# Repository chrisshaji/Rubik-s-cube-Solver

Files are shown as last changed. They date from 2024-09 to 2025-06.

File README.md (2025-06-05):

# Rubik's Cube Solver

Fully 3-D printed rubik's cube solver that can solve a 3x3 rubik's cube.

## Design Rationale

The motor and cube connectors were the first pieces to be designed and fabricated. These pieces had to be tolerenced perfectly as if they were too loose, it would slip and too tight 
then it would be really hard to remove it. After a lot of testing and printing, I arrived at the perfect dimensions that ensure a smooth fit with minimal sliding. Moreover, in order
screw holes were implemented on the side in the offchance that these piece rub on each other and get loose after a lot of testing.

The main design constraint was coming up with a solution to securely harness each stepper motor to each face of the cube. Each motor weighs ~1 lb so 
so the column pieces had to be strong enough to support it while vibrating at max speed. The dimensions were measured using vernier calipers and a tolerance range of 8-10% was used.
I had also implemented a honeycomb design on the side for extra ventiliation. Finally, screw tabs were added so that motor can be screwed into the column. 

One goal I had with the base plate and the arch was to keep the filament usage down to a minimum. I have employed the use of pattern to hollow out these pieces so that less material would be used.
For the arch, I had initially envisioned to use neodynium magnets for easy removal of the cube. However, this proved not to be strong enough upon further testing, therefore I went with the good old 
screws and nuts on the side of the arch. For the base plate, similar design changes were made and each of the four columns, along with the bottom motor can be screwed directly onto the base plate.

<table align="center">
  <tr>
    <td style="padding-right: 30px;">
      Breadboarding the motors
      <br>
      <span>Breadboarding the motors</span>
    </td>
    <td style="padding-right: 30px;">
      Motor screwed into the arch
      <br>
      <span>Motor screwed into the arch</span>
    </td>
    <td>
      Assembly rendered in SolidWorks
      <br>
      <span>Assembly rendered in SolidWorks</span>
    </td>
  </tr>
</table>

## Fabrication
The enclosure, connectors and motor holders were fully 3d printed on my Elegoo Neptune 3-pro printer using PLA and sliced using Cura. The trickiest part to print by far was the base plate since it took up whole build volume of my printer. The first time I printed it, I ended up with a mess since I forgot to properly configure the bed adhesion setting for tree supports in Cura.
### Print Settings:
  - Nozzle temp : 210° C, Heatbed : 50° C
  - 10% infill on base plate with 3 walls
  - 15% infill and 2 walls on other parts
  - Tree supports for the base plate

<table align="center">
  <tr>
    <td style="padding-right: 20px;">
      Caption for Image 1
      <br>
      <span>Base Plate Print ~24 hours <span>
    </td>
    <td style="padding-left: 20px;">
      Caption for Image 2
      <br>
      <span>Failed due to poor adhesion :(</span>
    </td>
  </tr>
</table>

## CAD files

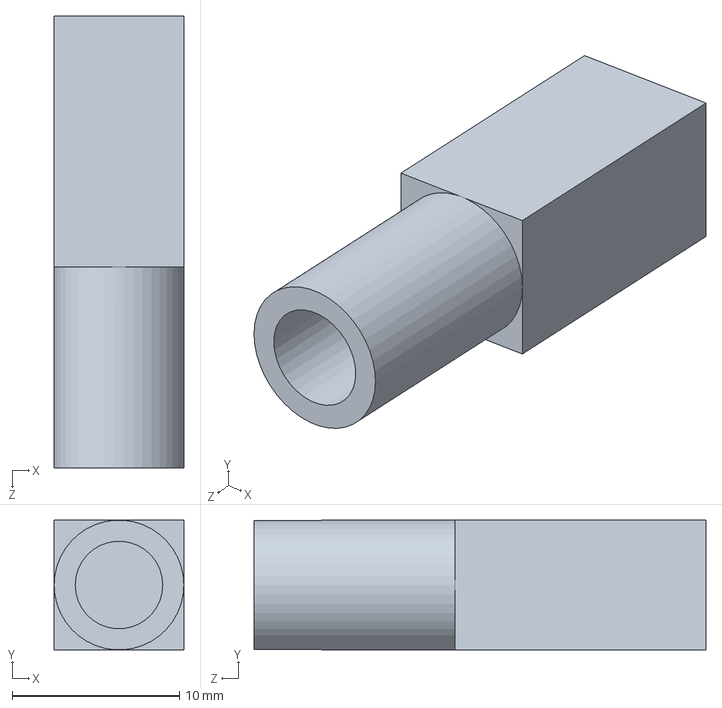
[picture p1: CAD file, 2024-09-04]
motor connector.SLDPRT
7.75 x 7.75 x 27.0 mm

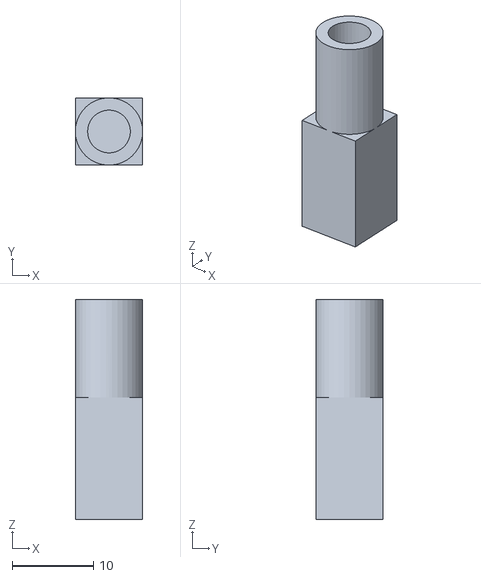
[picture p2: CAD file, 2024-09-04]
STL files/motor connector 525.STL
8.27 x 8.27 x 27.0

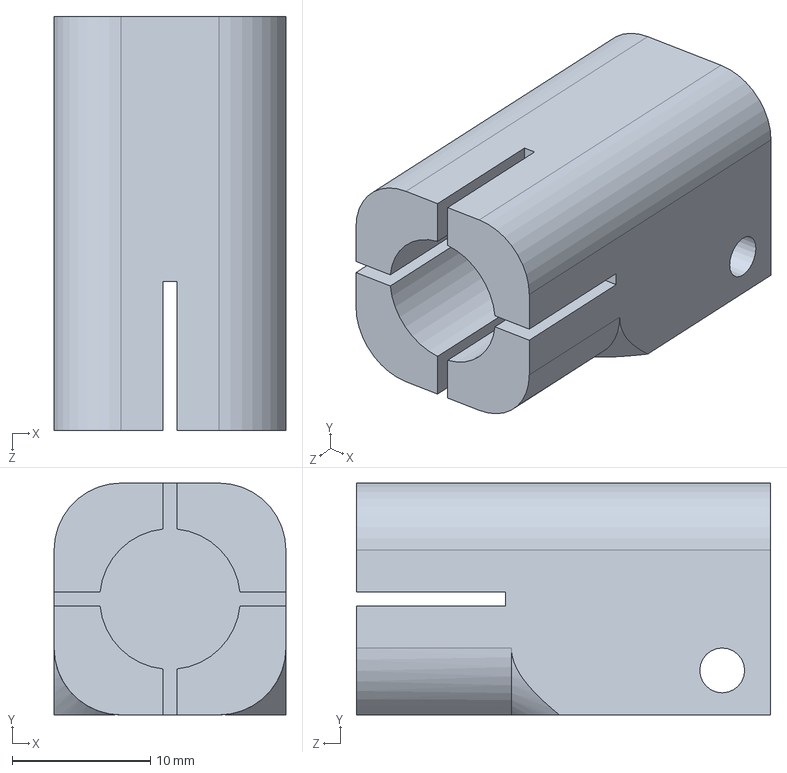
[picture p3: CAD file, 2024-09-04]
cube connector.SLDPRT
16.8 x 16.8 x 30.0 mm

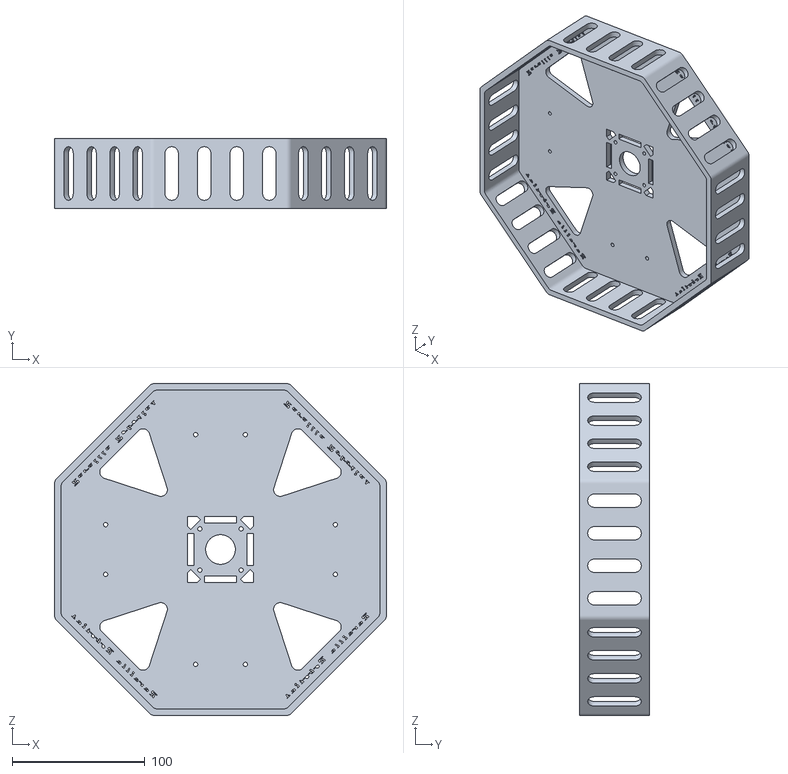
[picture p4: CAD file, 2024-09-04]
STL files/Base plate 2 new.STL
250.0 x 52.5 x 250.0

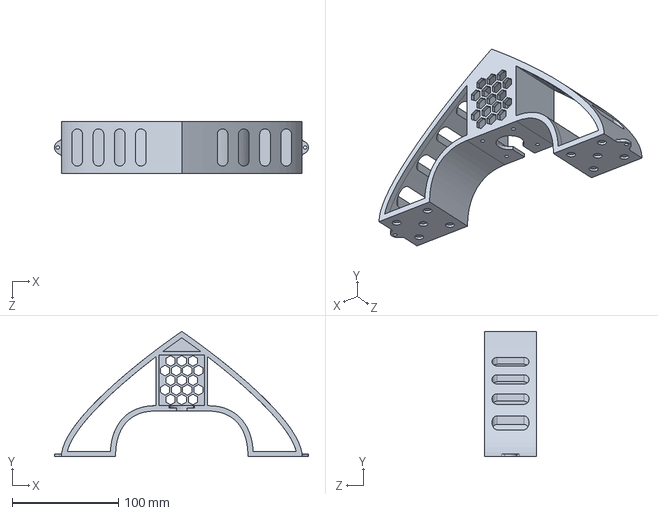
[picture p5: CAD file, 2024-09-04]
arch v2.SLDPRT
239.5 x 118.0 x 49.0 mm

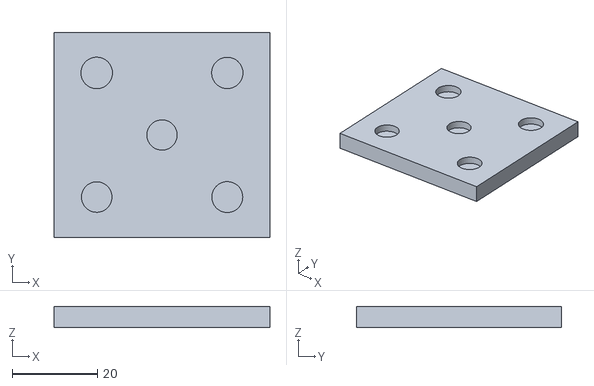
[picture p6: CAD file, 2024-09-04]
STL files/magnets testing.STL
50.6 x 48.1 x 5.00

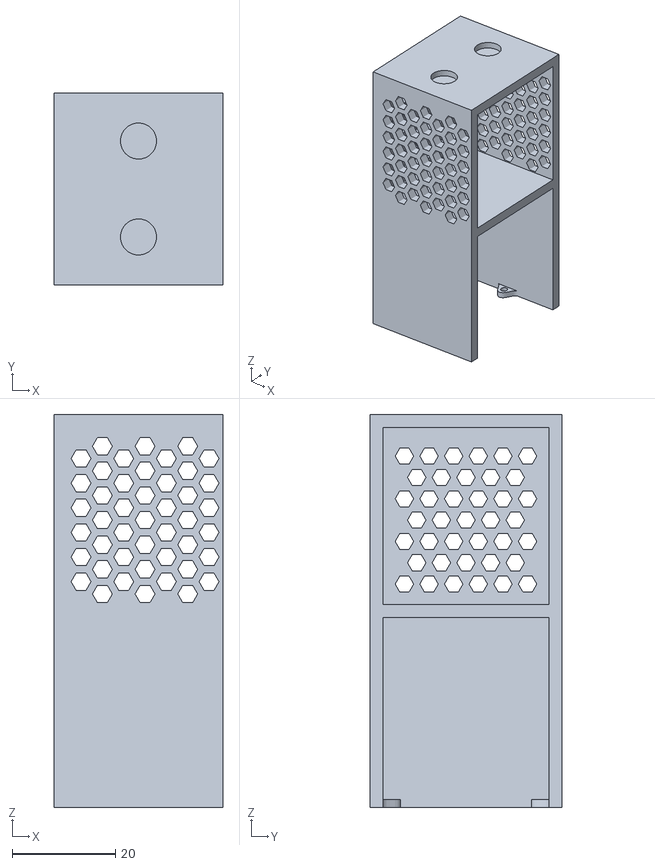
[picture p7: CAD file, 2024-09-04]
STL files/holder type 1.STL
32.7 x 37.2 x 76.2

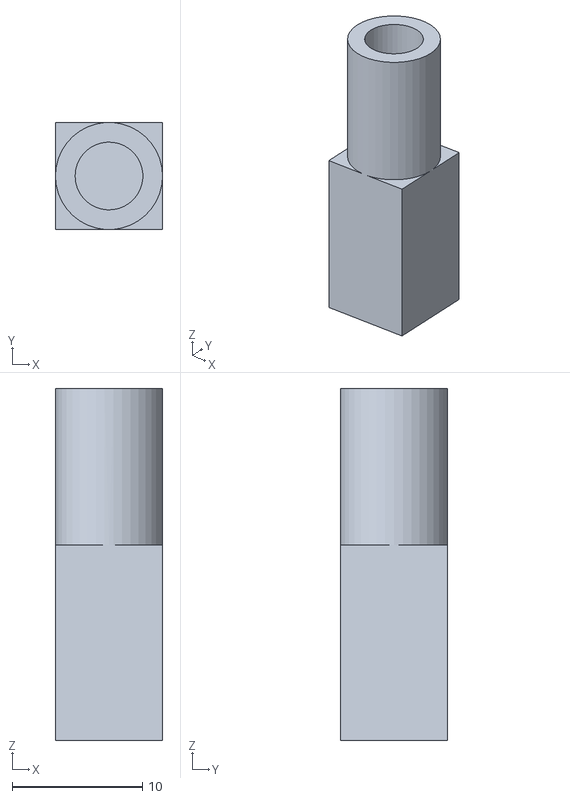
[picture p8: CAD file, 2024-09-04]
STL files/motor connector v2.STL
8.22 x 8.22 x 27.0

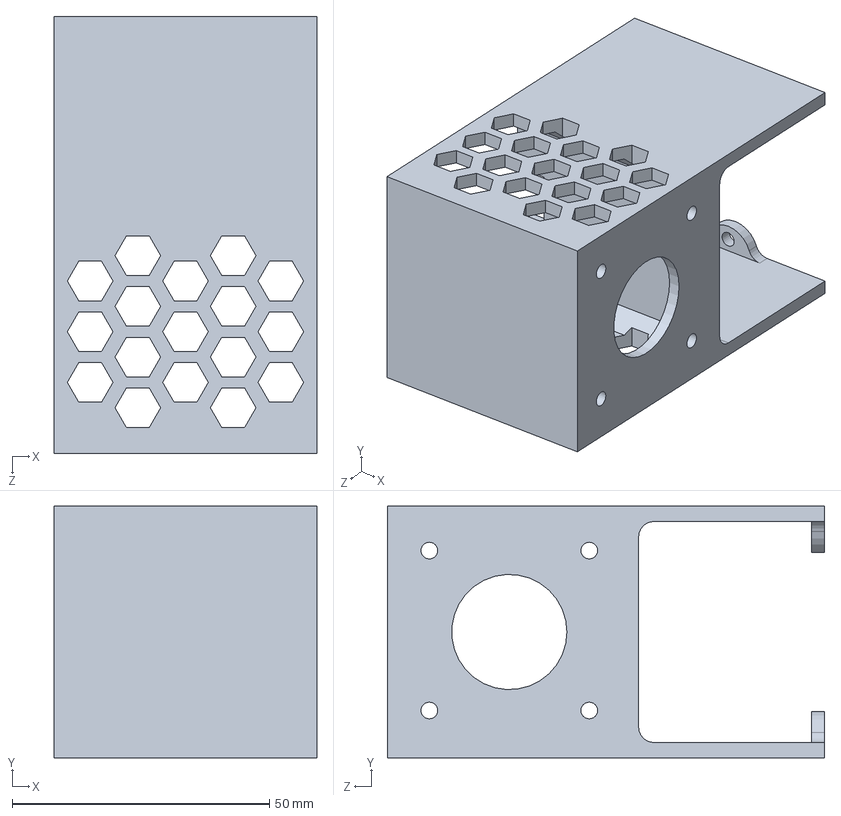
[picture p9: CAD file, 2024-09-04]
holder type 2 - no magnets.SLDPRT
51.0 x 49.0 x 85.0 mm

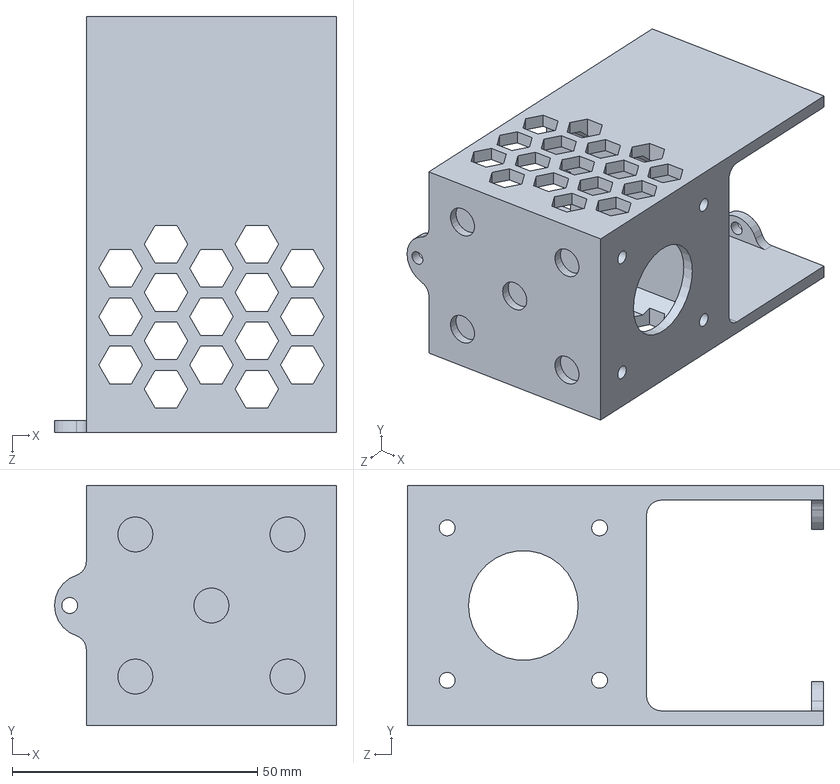
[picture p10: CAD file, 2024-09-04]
holder type 2.SLDPRT
57.5 x 49.0 x 85.0 mm

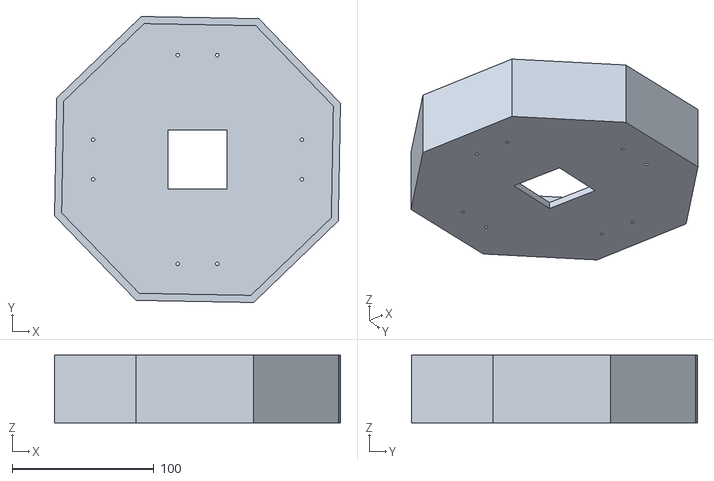
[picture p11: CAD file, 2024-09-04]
STL files/Base plate.STL
202.0 x 202.0 x 48.0

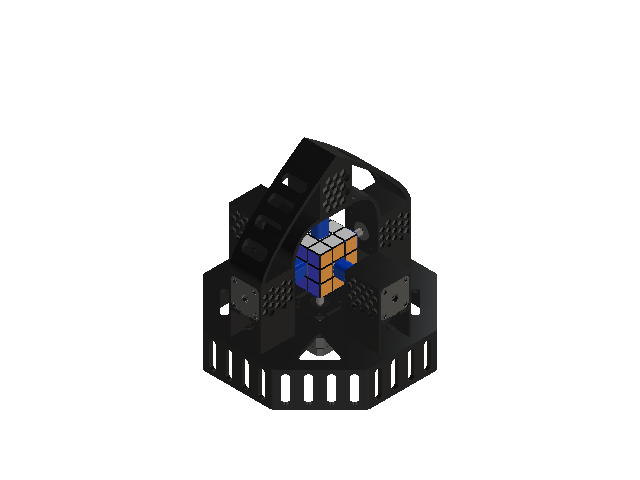
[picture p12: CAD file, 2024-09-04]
rubix cube assem.SLDASM
holder type 2 x 2
arch v2
Base plate 2
6627T91_Stepper Motor x 6
cube connector x 6
motor connector x 6
Core Part
Center Part-Y
Center Part-B
Center Part-G
Center Part-O
Center Part-R
Center Part-W
Edge Part-BO
Edge Part-BR
Edge Part-GO
Edge Part-GR
Edge Part-WB
Edge Part-WG
Edge Part-WO
Edge Part-WR
Edge Part-YB
Edge Part-YG
Edge Part-YO
Edge Part-YR
Corner Part-W-BO
Corner Part-W-BR
Corner Part-W-GO
Corner Part-W-GR
Corner Part-Y-BO
Corner Part-Y-BR
Corner Part-Y-GO
Corner Part-Y-GR
holder type 2 - no magnets x 2

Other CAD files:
Base plate 2.SLDPRT
STL files/testing magnets.STL
STL files/motor connector 523.STL
STL files/Base plate 2.STL
STL files/arch v2.STL
STL files/cube connector.STL
STL files/holder type 2 - no magnets.STL
STL files/holder type 2.STL
STL files/motor connector.STL
